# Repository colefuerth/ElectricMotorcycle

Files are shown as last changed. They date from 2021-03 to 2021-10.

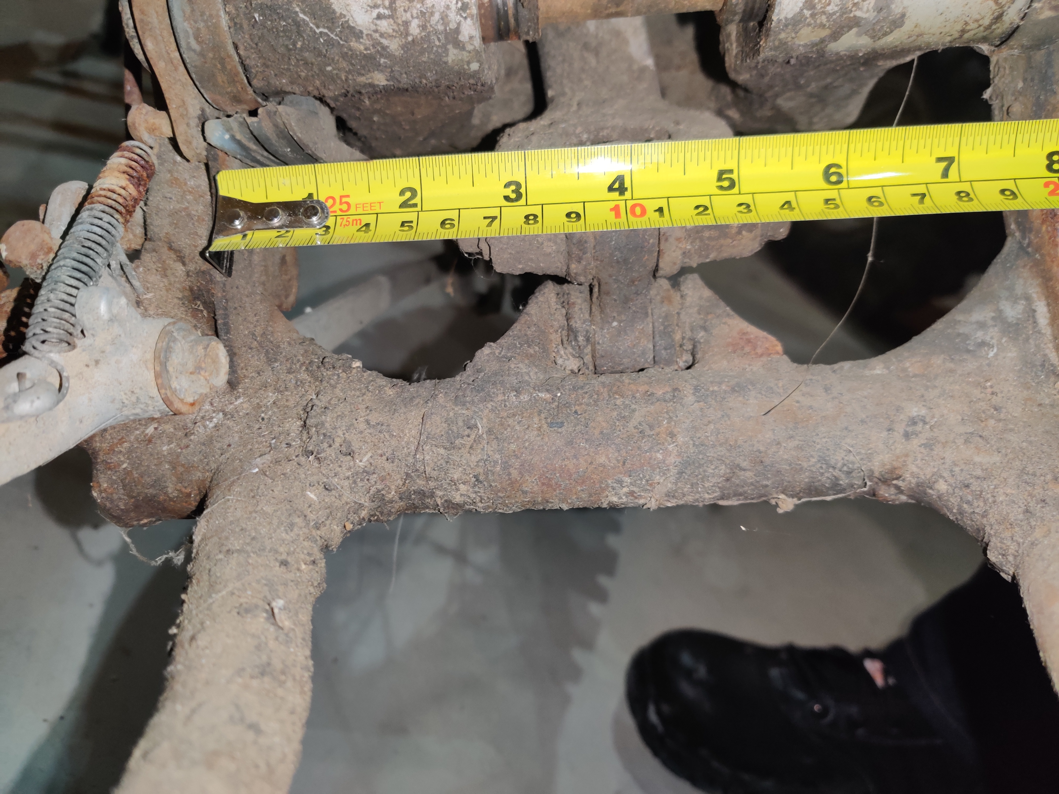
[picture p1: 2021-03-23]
Documentation/Mechanical/Mechanical pictures for Reference/IMG_20191113_204941.jpg

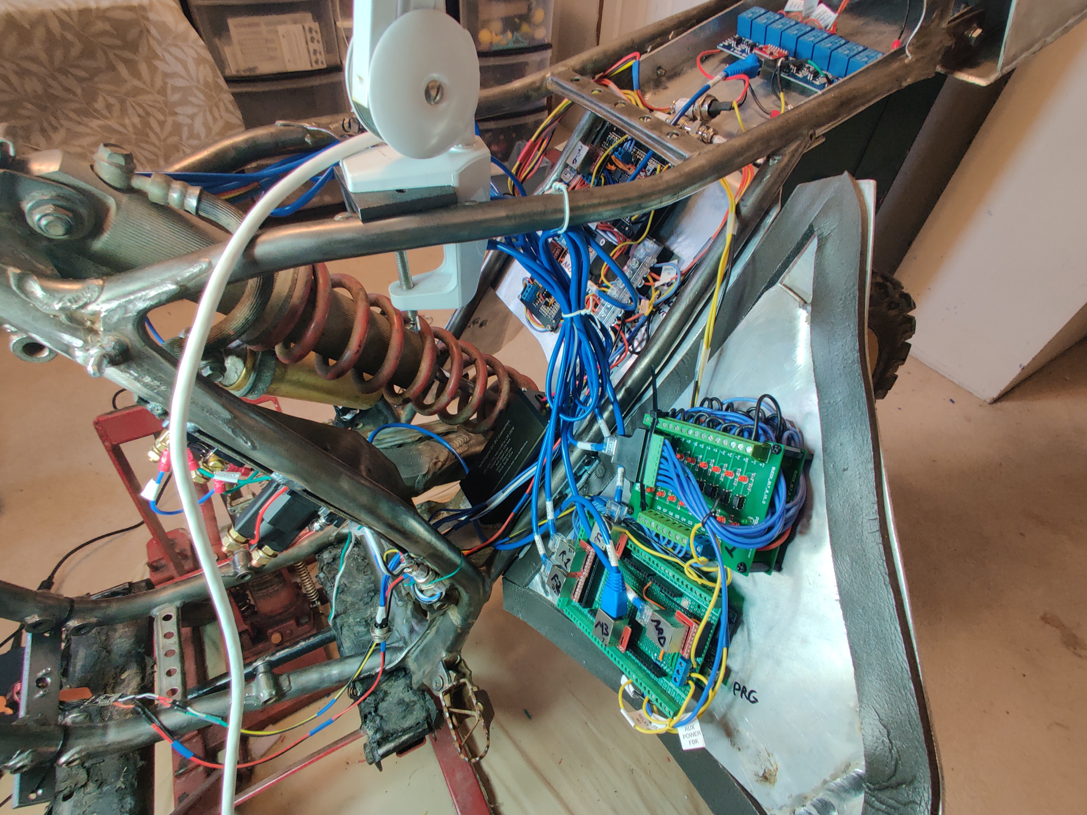
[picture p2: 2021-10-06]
Cole Fuerth Project Photo Repository/Wiring/Left view, panel open.jpg

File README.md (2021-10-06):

# ElectricMotorcycle

This was my Electronics Engineering Technology capstone project. 

A fully-electric dirtbike, built using an Arduino Mega.

### Key Features:
 * Fully-custom analog sensing boards, using OPAMPs and voltage protection for the Arduino
 * Custom firmware, written from scratch'
 * Electrical systems all designed by hand, with current safeties, and ALL IO is isolated in and out of the processor, to remove electrical noise.
 * Modular removable panels, with quick disconnects. Each panel comes off with four screws, and at most three connectors
 * Fully custom charging circuit and battery management
 * Touchscreen HMI, displaying telemetry and hosting a few settings, and a faults window
 * LOTS of faults, for communications, voltage, current, temperatures, safeties
 * Info prompts for when a safety stops the system from going into 'D' (drive)
 * Safety systems, disconnects on any major faults; main safety relay disconnects by a hardware-controlled switch, in case of processor lock-up
 * All lights and features required to make the bike road-legal

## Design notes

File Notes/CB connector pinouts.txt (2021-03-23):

PINOUTS FOR CB CONNECTORS

to arduino panel:
1 - GND
2 - ARD 5V
3 - 5V for HMI and RS3231
4 - spare

to central panel:
1 - GND
2 - 5V
3 - 12V to shunt input
4 - 12V rail

main power to central panel
1 - GND
2 - Vbat+
3 - motor shunt
4 - pwm motor control

cell levels
1 - cell 1
2 - cell 2
3 - cell 3
4 - throttle out

to rear fender:
1 - GND
2 - 12V
3 - 5V
4 - spare

to front panel
 - i didnt record these lmao

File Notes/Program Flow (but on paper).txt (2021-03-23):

-- PROCESSOR BOOTS --

<declare all variables>
	- include DS3231 libraries
	- define color values for nextion
	- define comm header byte for nextion
	- define serial port for nextion
	
	- declare function call memory bits (ONS,Timers,ToggledMemory)
	
	- declare arrays for opto inputs
	- declare constants for opto input pins
	- declare pointers into the opto arrays
	- declare speed px input and input pin

	- declare array for analog input values
	- declare constant arrays for analog input pin values
	- declare pointers into the analog data array

	- declare arrays for digital/relay outputs
	- declare constant arrays for relay output pin values
	- declare pointers into relay arrays

 	- declare misc variables for modes, clockRoutine, driveSystem, monitorSystem

	- declare a boolean array for active faults flags
	- declare a constant array for fault levels
	- declare a constant string array for fault messages
	- declare misc fault variables
	- declare pointers into the boolean fault flags array

	- declare misc variables for supporting my nextion functions in place of nextion libraries

	- declare misc debug bits and memory

-- PROGRAM START --

<SETUP>
	- check if aux 5v power is on, if off, processor disables all external IO

	- setup serial to PC if debugging is enabled
	- setup setial to nextion if nextion is enabled
	- setup RTC if aux power is detected

	- declare all IO pin modes (input/output)
	- write a 1 (relay off) to all relay output pins
	- put constant power on pins providing power/gnd to relay opto isolators

	- reset logic states on onshots, toggles, and fault flags

	- record the amount of time it took to complete setup and display to serial

	- do an IO update before starting the first scan

<LOOP>
	- Reset tracker bits for ONS and timers
	- set io update pulse (50Hz pulse triggers routine io updates)
	- Call MapInputs
	- call MapOutputs
	- call LightRoutine
	- call DriveSystem
	- call MonitorSystem
	- call HMIControl
	- call debugRoutine
	- call Faults
	- if firstscan, reset firstscan bit

<MapInputs>
	- if 50Hz pulse is true, do an IO update, else, update speed px state and return
	- every 50hz pulse, update all opto digital inputs and throttle analog value
	- every 50hz pulse, update one of the 7 nonessential analog pins, cycling through each time

<LightRoutine>
	- If lights are off, turn off all light bits, update horn status, and return
	- set turn signals using a flasher bit if their respective side is true
	- if a turn is false, front idles at true and rear idles at false
	- Set brake, headlight, and fog light outputs accordingly
	- set horn output accordingly

<ClockRoutine>
	- if aux power is on, update RTC value

<DriveSystem>
	- System will not go into gear unless:
		- killswitch has been off at least once since boot
		- killswitch is on
		- all essential connections are OK
		- throttle is at idle
	- check if killswitch has been off since boot
	- Main motor controller contactor will only be closed if:
		- killswitch has been off since boot
		- no level 1 faults are detected
		- killswitch is on
	- map throttle output based on ingear and killswitch statuses
	- map throttlePercent for monitoring/fault purposes based on throttle input value

<MonitorSystem>
	- record watchdog value
	- update longest/fastest cycle values
	- calculate current draw on motor and 12V shunts from analog IO
	- update total draw in mAh based on motor shunt reading
	- update vBat value
	- update individual cell volt values
	- update front wheel speed from speed PX

<HMIControl>
	- check for button presses from nextion
	- update fault window buffer
	- update elements on the current page only, one at a time on a 50hz pulse, and only update if the value has changed from the last update on that element, or if the current page has changed since the last update on that element

<MapOutputs>
	- Update outputs if:
		- an IO update request pulse is read
		- aux power is on OR debugging is enabled

<Faults>
	- Check for a fault reset request, if true, reset all fault flags
	- check for com errors to opto boards, or either side handlebar controls
	- check watchdog (set for 100ms)
	- check that throttle value is within bounds (0.5V to 4.5V)
	- check for overflow on ONS bits
	- Check that individual cells are above lithium storage voltage, else throw a warning
	- Check that individual cells are above lithium critical voltage, else throw a level 1 fault
	- check for any faults present
	- check for any level 2 faults present
	- check for any level 1 faults present
	- count number of active faults
	- display faults to serial if debugging is active on a PET
	- check if aux power has failed
	- check if number of timers or oneshots has changed since previous scans, if yes, throw a level 1 fault
	- if first scan, record values of timer and ONS tracker bits at the end of scan

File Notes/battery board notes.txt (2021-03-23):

heaters blow at constant current over 3A

If I use these in 6S, 4P:

6*16 = 96V

3A * 4 = 12A

96*12A = 1152V

 - using the thermocouples is NOT an option; they will blow all the time
 - ktm e-xc is 3.9kwh and lasts about an hour and a half; 3.9kwh / 1.5h = 2.6kw
 - 2600kw / 96v = 27A constant current
27A / 4P = ~7A
27A / 5P = 5.4A constant

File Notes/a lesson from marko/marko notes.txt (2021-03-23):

CA3140E single ended opamp pin compatible with lm741

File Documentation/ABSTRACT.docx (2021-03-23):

ABSTRACT

The EET Capstone project, “Control System for an Electric Motorcycle”, is a project designed to control a fully electric motorcycle, with lithium-ion cells, a charging circuit, an electric motor/controller, and safety and monitoring systems using an Atmega 2560 processor. This system uses amplifiers, optocouplers, relay boards, voltage converters, an EV controller, lithium balancing circuits, and several more systems to create a ‘smart’ system for monitoring the status of the system. Both the user via the physical killswitch, or the processor, with a relay killswitch, will be able to disconnect the battery from the EV controller. Individual monitoring systems on-board include:

- Current monitoring of a 12V supply
- Current monitoring of total draw from battery, up to 150A
- Monitoring of individual cell voltages, each cell is 4S lithium, and 4 of those in series
- Monitoring of total current draw from the battery in mAh
- Monitoring of the front wheel speed
- Monitoring of the total battery voltage
- Monitoring and recreation of the throttle value

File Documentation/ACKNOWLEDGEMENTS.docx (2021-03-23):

ACKNOWLEDGEMENTS

There are a few key people that were important in the design and fabrication of this project.

First, my friend Scott MacKay, who was around for the entire mechanical build of the project; he did most of the cutting and shaping of aluminum and steel, and all of the steel welding. The panels would not have turned out as well as they did without his help, and he was around for many, many hours during build.

My father, Brian Fuerth, welded the rear fender, and cut the front panels where the headlights and charging circuits are. He took an interest in the mechanical construction, and he will be helping with construction of the drive system of the bike, including motor and controller mounts, and a chassis for batteries.

Al Repmann is another individual who helped, he did most of the aluminum welding with his spool welder and some Tig welding.

Marko Jovonovic and John Schlichther were some individuals I consulted on opamp design, which were issues I would not have been able to efficiently tackle myself.

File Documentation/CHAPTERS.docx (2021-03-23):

Introduction

My name is Cole Fuerth, and for my Electronics Engineering Technology capstone project, I built a control system for an electric motorcycle. This project, unlike most of its peers, does not have a set cycle or repeated function. Instead, my system monitors ongoing telemetry, and uses input from the user and peripheral devices, to safely control an electric vehicle, with some safeties, and a basic throttle control. This system monitors total battery voltage, as well as the voltage of individual lithium cells, and the current draw of the total system from a 60VDC source, and the current draw of the control system at 12V.

The biggest challenge of creating this system is creating a safe and reliable interface between a 5V TTL ecosystem, a 12V control system, and a 60V drive system. Instrumentation amplifiers and operational amplifiers are used for measuring and isolating analog input and output signals with the Arduino Mega controller, and opto-isolators isolate the 12V inputs, while opto-isolated relay packs handle 12V output control, and some control of the EV Controller functions, in place of switches.

Much effort was put into hardware safeties. One of these important features is the ability to monitor individual cell voltages. Lithium cells can be dangerous when misused, so if a heater safety is tripped on a cell in parallel with others, or one cell has a much higher internal resistance than others, the load is not evenly distributed, and there is a discrepancy between capacities of the cells in series. This can become a big problem in the short and long term, as it is important all the cells wear evenly in a system with 200 lithium cells networked together.

Overall, I am very proud of this achievement in creating this project, and although the conclusion of the Capstone approaches, this system will continue to grow and improve as its use continues long past the conclusion of EET 617.

System Design:

Processor Logic Layout

Since the processor needs to handle and map a large volume of information within and outside its architecture, arrays were used for data handling, and referenced locations within these arrays by defining pointers into the arrays to access information when it was needed. This proved to be a very effective system, as the code was very messy and hard to understand before this system was implemented. This allowed handling of all the IO at once when mapping inputs and outputs, by defining arrays in global memory for storing the status of bits and integers being used, along with their corresponding hardware pins when applicable.

Within the main program loop, all logic is done within subroutines, and all subroutines are called within the loop. This allows the separation of logic into routines with a specific task, so one task can be skipped according to user settings, for example, the LCD display can be disabled in settings.

The program starts with importing libraries for the DS3231 (Nextion libraries were scrapped, and replaced with methods that were developed (because the stock Nextion methods were too slow), then definitions, followed by all global memory declarations, including arrays, settings, and pointers into arrays, and misc global memory used to support methods, and then the main program flow. The program starts by running the setup() method, which sets up auxiliary devices and digital IO based on user settings and feedback from auxiliary power, and sets any status bits that need an initial value before the main program cycle begins. After setup completes, the processor begins looping the loop() method, which calls all of my methods I created to handle the vehicle functions.

Methods

Many processes within the logic are repetitive, so methods were created to promote efficiency. A method is a section of code that can be called with or without parameters, that returns either void or a variable defined with the method. This resulted in much cleaner memory management, and an easier to understand program. A good example of this format is my OneShot logic. There are 32 globally available oneshot bits, as well as 32 dedicated to each fault, for displaying fault messages once when a fault goes true. OneShot are managed automatically, with a tracker that is reset at the end of every cycle, and every time a oneshot is called, that bit is incremented, so the call will adapt to the number of oneshot calls used.

Other calls were created for things such as writing Nextion values and settings, whose process is detailed below in the Nextion HMI Display section.

Other examples of methods created are voltage to analog translations, which would be able to convert back and forth between floating point voltages, and integer values for either analogRead or analogWrite values, an on timer, or ‘TON’, a limit method that returned a Boolean, similar to that used in PLCs, and methods for addressing button presses on the HMI.

There also exist methods for returning string values; one is called every scan and cycles through active faults, to be displayed on general information pages at the top in a fault window, and another generates a list of the top 10 active faults sorted by priority, which can be returned individually by requesting spot 0-9, to be displayed in a list of faults on a window in the HMI.

Fault Handling

A Fault-oriented safety system handles safety processes, with a motor contactor that can break the connection between the battery and the EV controller. This connection is broken either by the processor via a relay when a Level 1 (Highest level) fault, or a throttle input exception is detected. The contactor coil is connected in series with a control relay, and a kill switch on the handlebars, so that if the processor freezes, the user still has a hard-stop to kill power to the motor. A level 1 fault is defined by a critical program fault in my functions, such as a miscount of automatically handled functions like ONS or Timers, or connection via RJ45 to the handlebars is lost, or throttle input leaves the acceptable range. A level 1 fault is a fault that requires a disconnect of power to the EV controller. The processor uses a watchdog to ensure IO updates are occurring fast enough to be reliable, and if deemed unreliable, throws a level 1 fault.

Faults are handled with an array of fault flags, differentiated by pointers that point to their memory bit within the array. Parallel arrays to the fault flag array contain information on fault level, as well as a message to go along with the fault when it is flagged.

Analog inputs

Operational Amplifiers were used for analog signal isolation in and out of the processor, chosen for their reliable electrical isolation between input and output, and their ability to only repeat an analog voltage within the supply rails.

A stack of custom soldered breadboard circuits handles all analog signals between the Arduino processor and the rest of the system. This includes total battery voltage, voltage on each of the four 4S Lithium cells in series that make up the battery, signal levels from the two current shunts, and throttle input and output levels.

Current levels are determined using current shunts, which are very low resistance resistors, that are made to an extreme level or precision, and to a certain spec. An example of this spec would be, that my 12V shunt is rated to 75mV at 15A across the shunt. This means, when the shunt is passing 15 amps of current, it will cause a potential drop of 75mV. This potential difference is the analog signal that is processed by my stack.

Analog values are processed by Instrumentation Amplifiers in the stack. The type of amplifier used was an INA126P. This amplifier is fed rail voltages of +16V and -9V, so that any and all analog readings on the input pins are well within the rail voltages, ensuring accuracy. The default gain on an INA126P is 5, and the output potential of this package can be represented by: V_(out) =(in_(+) -in_(-) )*(5+(80kΩ)/(R_G)) . In the case of a very low input differential, getting an accurate and useable output means we need a gain resistor, R_G . R_G was calculated for the 12V shunt, for example, by substituting the maximum current reading signal level as the voltage differential, and the maximum output potential desired on the Arduino input as V_(out) (4.50V), and solving for R_G . The closest value to the result that could be produced with the parts on hand was 1.47kΩ , which would produce a potential of 4.425V at 15A through the shunt. A similar process was followed for the 50mV 150A shunt for measuring current directly at the battery negative terminal, which calculated an R_G of 1kΩ .

Voltage levels on individual cells were collected using INA126P amplifiers and voltage dividers. Each cell node was divided, so that the four levels, spanning from ground to cell 4, were at a potential of 3.4V. This meant that, the potential drop across each cell after the voltage divider was about 0.85V. After using these references to generate a signal for each cell voltage through INA126P Instrumentation Amplifiers, the optimal signal level for each cell was approximately 4.25V. This level is easily and accurately able to be read and mapped to a real voltage level for the Arduino to use, and display to the user.

The schematic of the four cell voltage sensors:

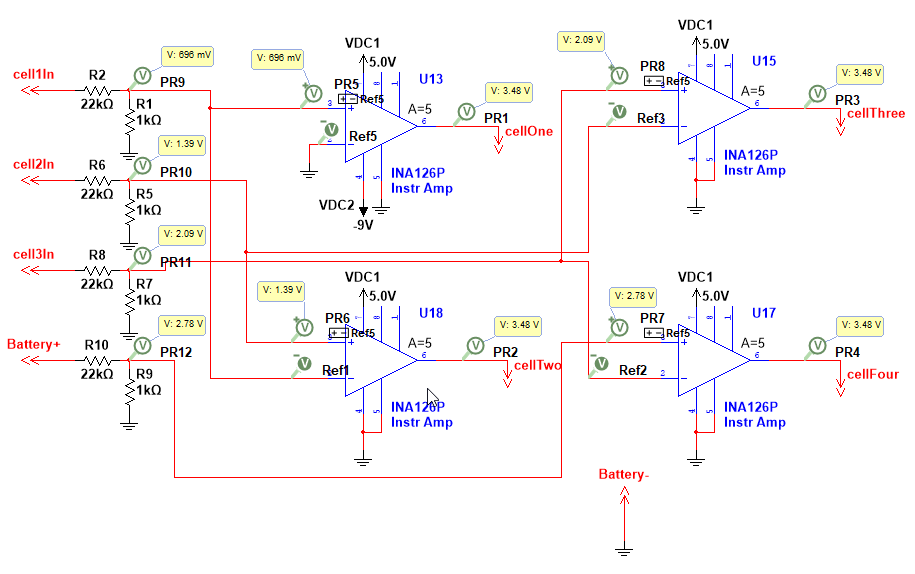
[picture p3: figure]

Figure 5-1

The total battery voltage was read using a voltage divider, same as above, so the battery voltage signal at 68V (charged), was 3.4V.

All analog inputs were buffered through CA3140 op amps, which provided reliable electrical isolation, and are linear op amps matching the pin configuration of LM741s, while being able to reliably operate close to the rail voltages, making them very useful as buffers.

The EV controller

The EV controller used was a 9kW CA Controller. This controller operates between 48V and 100V DC, and controls a brushless motor. The inputs of this controller include an analog throttle reading of 1-4V, as well as wires used for selecting modes of operation by grounding the connections. The throttle signal is provided by a high-frequency (980Hz) PWM using duty cycle to control the DC level, which is passed through a CA3140 linear operational amplifier and a 2N4244 NPN transistor to provide electrical isolation, and a power amplifier capable of delivering up to 500mA. The controller does not sink this much current, but a CA3140 can only source 14mA of current, so a power amplifier circuit was implemented to avoid stressing the analog buffer. Control of the mode selection was accomplished using a relay pack dedicated to ESC control, which operates the motor contactor solenoid, as well as shorting out control wires as mentioned previously.

Light Control

Lights are controlled by 6-channel relay packs, at the front and rear of the vehicle. Lights all operate at 12V DC, and are controlled by the Arduino, using switches on the handlebars of the vehicle. The bike features a headlight and taillight, brake light, front and rear turn signals, and fog/trail lights. Some features unique to this bike from others is, most two-wheeled vehicles do not feature hazard lights or fog lights, or a master kill switch for lights, but these were implemented in this system. Fog lights are used at night, to light up the operator’s peripheral vision. The light kill switch is useful for power conservation, and it never hurts to be sneaky, especially on an electric vehicle, when noise is already at a minimum. Turn signals were added so that the vehicle could be safe when passing though an urban environment.

Speed Sensing

Speed sensing is done using an inductive proximity sensor picking up spokes on the front brake disc. The front wheel has a 70cm outer diameter, and there are 8 spokes on the disc. Using the outer diameter, the wheel RPM was calculated at different speeds, and then using that information, the positive pulses per second could be determined at different speeds. The points found were at 100km/h, the wheel rotates at 12.64RPM, and generates 101 pulses per second, so ~10ms between each pulse, and at 25km/h, there would be 40ms between each pulse. A map() method was used with these two points for reference, since the relation is linear, to generate a value in km/h by measuring the time between each positive edge trigger from the PX to calculate the speed of the front wheel.

Nextion HMI Display

Design of the HMI display took a long time, as the system started with attempts to use a TFT display, driven by an Arduino Mega. This approach proved inefficient, so a different platform was adopted. Nextion is a very polished system, in relation to its competitors in the Arduino community, and proved to be easy to develop, thanks to its GUI interface for development. The stock Nextion libraries were unreliable and slow, so custom libraries were developed by studying how the default libraries would handle incoming and outgoing data, and replicating that serial format to create custom libraries designed around the vehicle’s ecosystem. This method proved much faster and more reliable, and stopped the processor from ‘hanging’ during serial transfers, like it did when using the stock libraries.

The Nextion display has three screens: a main screen, an alarms screen, and a statistics screen. The ‘MAIN’ screen only displays essential information in a larger font, for ease of use on the go. The ‘ALARMS’ screen displays up to ten active alarms, in order of importance. The ‘STAT’ screen displays more information than the main screen, in a smaller font, for active monitoring of telemetry within the system.

The system is optimized such that, only elements on the current page are updated, and only one element is updated at a time. Elements are also only updated when the value changes from the previously written value, using a buffer. Further optimization was achieved by changing the BAUD rate on the Nextion from 9600 to 115200, using a custom method.

Drive Safeties

The vehicle was designed such that, in order to arm the vehicle, a certain set of conditions must first be met. Firstly, the kill switch must be on. Secondly, the kill switch must have been in the ‘open’ position at least once since boot, to prevent accidental arming on boot. Thirdly, the throttle must be at idle when the start PB is pressed, in order to arm the motor. Any level 1, or ‘critical’ faults, will automatically open the motor contactor.

Charging Circuit

A charging circuit was implemented, to avoid disassembly of the battery pack for charging. Each 16S pack is made up of four 4S Li-Ion packs in series, so when in operation the pack operates as a 16S 5200mAh battery pack, but when in charging mode, an 8-channel relay board is provided power, and all four of the 4S packs switch into a parallel configuration, on a different connector than the one used for normal operation. This allows for charging of all the packs at once, without disassembly of the entire battery assembly. When no power is applied to the relay packs, the pack defaults to the NC contacts, and the pack is once again in a 16S series configuration.

A dedicated 5V rail and charging rail are entirely isolated from the normal, operating circuits, so in charging mode, the cells are completely disconnected from the system.

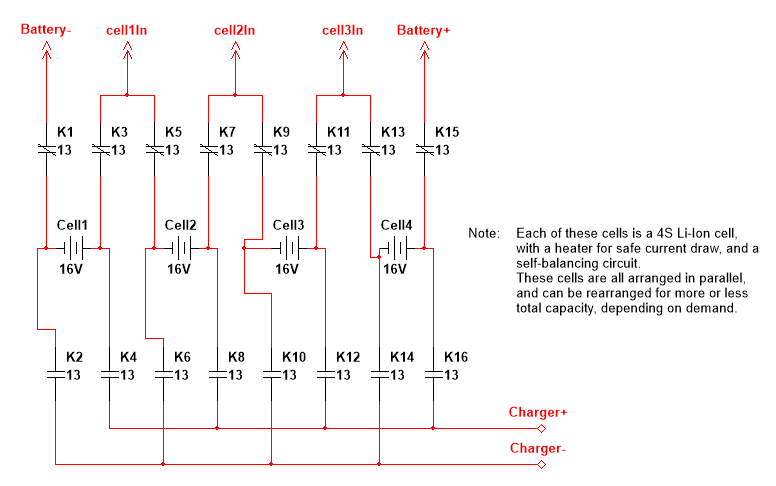
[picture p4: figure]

Figure 8-1

Background Theory:

Instrumentation Amplifiers

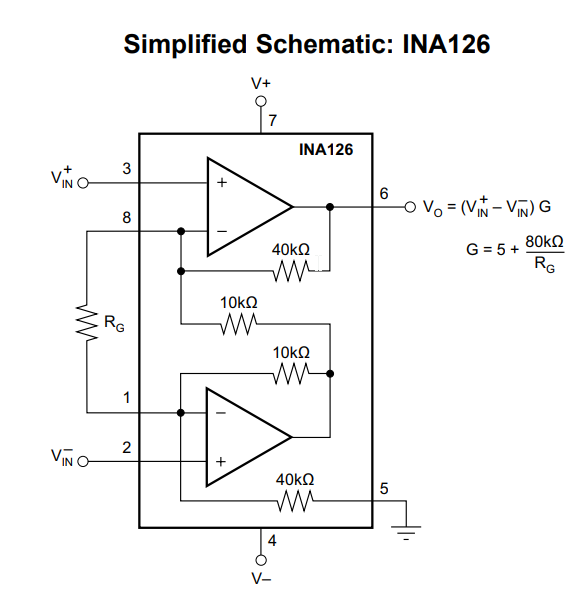
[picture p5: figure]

An instrumentation amplifier is a type of operational amplifier that produces an output signal proportional to the difference between two input pins. The instrumentation amplifier used was an INA126P, which is an 8-pin op-amp package, which has a pin configuration compatible with standard solderable boards, or breadboards. Both inputs must be within a ±0.7V range outside of the supply rails, so a negative and positive supply greater than the range of inputs is recommended, but the INA126P is a package capable of single-ended operation, meaning that the negative supply rail can be grounded, and the package will still behave reliably. The package is capable of up to ±18V supplied, or a 36V difference in potential between the supply rails.

Figure 9-1

Output potential on pin 6 of this package can be calculated with the formula:

V_(out) =(in_(+) -in_(-) )*(5+(80kΩ)/(R_G))

R_G is a gain resistor, connected across pins 1 and 8. With no gain resistor, this package defaults to a gain of 5, but when a higher gain is desired, output can be amplified. This is especially useful when conditioning a signal from a current shunt.

Linear Operational Amplifiers and Power Amplifiers

The CA3140 Operational Amplifier is a package matching the pin configuration of an LM741, but able to reliably operate on a single-ended supply, and still reproduce an analog signal near the voltage supply rails. This characteristic is imperative in an analog buffer or power amplifier.

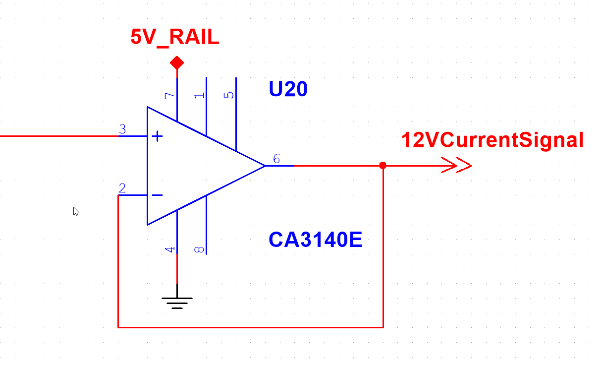
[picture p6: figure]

The CA3140 operates on a supply of up to 36V across the supply rails but is rated to operate reliably in a 5V TTL system.

The CA3140 can be configured as an analog buffer using the following schematic:

Figure 10-1

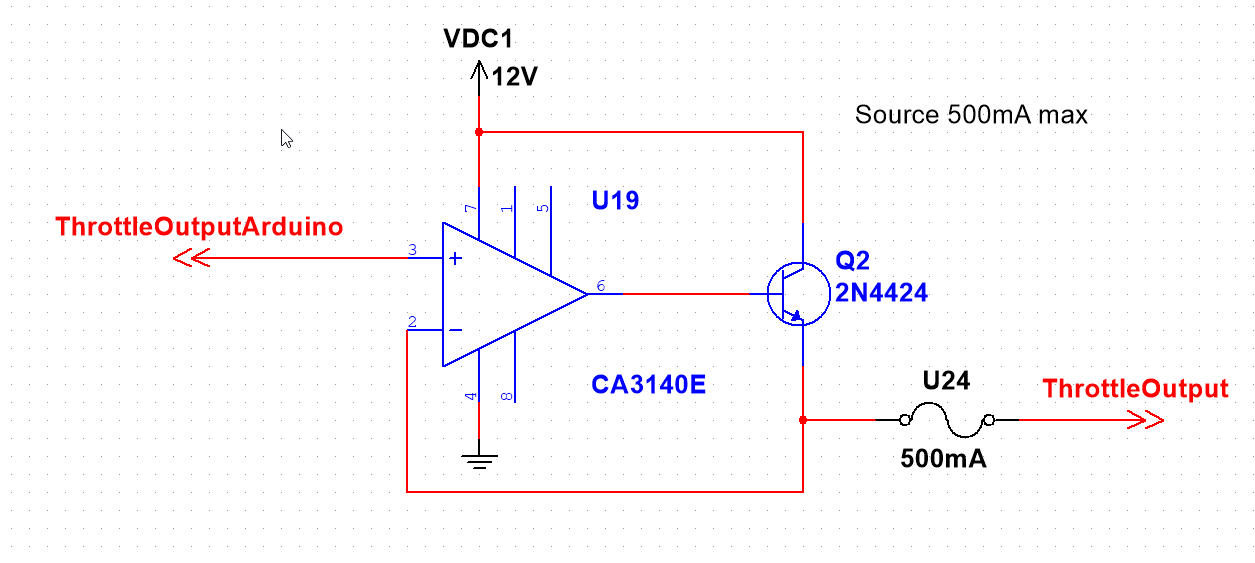
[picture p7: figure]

The CA3140 can only source up to 10mA maximum in a 5V TTL environment, so in a situation where this package is used as a voltage out buffer into a larger system, a power amplifier circuit is useful. Connecting the emitter of an NPN transistor package to the feedback (-) pin of the CA3140, the output of the package to the base of the transistor, and the collector of the transistor to the supply rail of the package produces a current supply of whatever the transistor is capable of, with the precision and isolation of the CA3140. This functionality can be accomplished with the following schematic:

Figure 10-2

The 2N4424 Transistor package is an NPN transistor capable of sourcing up to 500mA, so in this configuration, a TTL processor can provide a PWM DC signal via pin 3 on the CA3140, and have electrical isolation from the output, along with a 500mA current source available, should it be needed.

Voltage Dividers

A voltage divider is a small, simple circuit that typically ‘divides’ a large signal into a smaller, useable signal. In this application, voltage dividers are used to sample battery voltage levels, and step them down to a level able to be processed by TTL circuits.

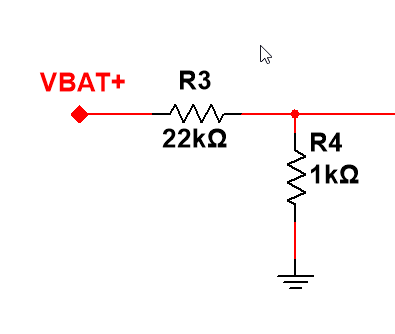
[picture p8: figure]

A voltage divider can be represented by the equation: V_(out) =V_(in) ((R_1)/(R_1 +R_2)) . For example, the total battery voltage is 68V, so the voltage divider used was R_1 =1kΩ , R_2 =22kΩ . This meant, the 68V input potential is reduced to 2.96V, which is well within the range of analog voltages handled in a TTL environment.

Figure 11-1

Opto-Isolators and Relays

Opto-Isolators and Relays are useful IO interfaces between a processor and external components in a control system. Opto-isolators utilize LED lights and photodiodes to provide complete electrical isolation between a processor and a control system, while operating at extremely fast speeds. Opto-isolator connections are typically active-low, meaning that when no potential difference is present across the inputs, the output to the processor is a TTL 1, but when a signal is detected at the input, a TTL 0 is sent to the processor.

Relays can be used together with optocouplers to provide two levels of isolation: The first level is the opto-isolated logic input from the processor, where a LOW signal is considered a logic TRUE. Then, an auxiliary power supply (5V, in this instance), will provide power to the relay coil when a TRUE signal is received, energizing the coil. The contacts on the relay can then operate up to a 250V / 10A control, providing complete isolation between the processor, 5V supply, and 12V control circuit.

Nextion HMI Libraries

The Nextion 3.2” Standard model was used as an HMI display. This model uses a GUI to design the interface, where different types of elements can be placed. These elements are each given an elementRef and a number to identify which element is which.

Serial communication to the Nextion is conditioned manually via a custom method, as the stock Nextion libraries are buggy.

A typical message to Nextion to set a ‘text’ of elementRef ‘t0’ is conditioned as follows:

‘t0.txt=”test”’ is sent using a Serial.print() command, followed by three Serial.write(0xFF) commands to signify the end of a message. All elements are set this way, by sending strings over serial to the Nextion followed up by ‘0xFF’ three times, which is then interpreted by the Nextion as a command.

Some other examples of Nextion commands used are:

Command | Descripton
baud=115200 | Sets the serial baud rate to 115200
t0.txt=”test” | Sets text element “t0” to “test”
b0.val=20 | b0 is a progress bar, which accepts any integer between 0-100
t0.pco=0x07E0 | t0 text element font color is set to green

Table 12-1

Nextion also sends serial messages to the Arduino on event of a button press, if the checkbox “send component ID” is checked for either a press or release event. This message is structured such that:

- Message begins with 0x65
- Three bytes follow the initializer, which represent, respectively, the page number, component ID, and event type (always 0x01 for button presses)
- 0xFF received three times in a row signifies the end of a message

Monitoring the serial buffer for messages in this configuration allows the processor to interpret serial messages from the Nextion HMI.

Conclusions:

Overall, this project, “Control System for an Electric Motorcycle”, although not perfect yet, has evolved over time. The initial features planned are mostly nonexistent here, replaced with equally advanced, if not more advanced, features that were deemed more important to operation.

Initial pulse check for light operation was removed and replaced with monitoring of the individual 4S cell voltages making up the battery pack. Odometer tracking was removed, as it is unimportant in an off-road vehicle, and was replaced with more advanced safety systems and faults.

One feature that was not finished because of hardware issues, was SD Card logging. This feature, although not present at the time of submission, will be completed later, as it is essential to debugging once the vehicle is in active use.

The panels and electrical build did turn out better than expected. The panels are sleek and formed to the shape of the frame and provide ample space for any and all electrical components mounted inside the frame.

Due to issues with suppliers, the drive motor and controller have not yet arrived, and will not be present at the time of demonstration and will be replaced by a small drone motor and controller, for demonstration purposes.

The system does have full lighting controls, as well as safe, isolated IO on the processor. Other features that were successfully implemented include analog sensing on electrical circuits throughout the vehicle, including 12V and Motor current readings, as well as total battery power and monitoring of individual 4S cell potentials within the 16S pack.

A lithium charging circuit was developed, built-in to the custom packs, to remove the need for disassembly when charging. This auto-switching charging circuit is a massive quality-of-life improvement.

The program is the largest section of the project; many standards were developed for it, and it has undergone 7 months of constant growth, refinement, and optimization. Although there are still some bugs and issues, they will continue to be addressed and this system will grow beyond the conclusion of this project.

References:

- Nextion send and received logic was copied from the Nextion master library, provided by Nextion on GitHub, and modified for efficiency and speed within the vehicle’s ecosystem. Core concepts of the code, although interpreted and structured using custom methods, and not exactly the original, were created by Nextion.

Bibliography:

- Nextion logic and examples were used to develop custom Nextion serial functions
- DS3231 Libraries were used for generating a time value from an RTC

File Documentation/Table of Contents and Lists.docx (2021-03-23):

Table of Contents:

Page | Section
i | Letter of Transmittal
ii | Title Page
iii | Declaration Page
iv | Table of Contents
v | List of Figures
vi | List of Tables
1 | Acknowledgements
2 | Abstract
3 | Introduction
4-10 | System Design
11-14 | Background Theory
15 | Conclusions
16 | References
17 | Bibliography
18-29 | Full electrical drawings
30-34 | Panel layouts
35-39 | Pin designations
40-41 | BOM
42 | Block Diagram
43-54 | Program flowcharts
55-78 | Full program listing

List of Figures:

Figure 5-1: | Schematic of Cell voltage sensors using Instrumentation Amplifiers and Voltage Dividers
Figure 8-1: | Battery pack schematic
Figure 9-1: | Simplified schematic of an INA126P Instrumentation Amplifier package
Figure 10-1: | Simple schematic of a linear op-amp buffer
Figure 10-2: | Schematic of a linear op-amp/transistor power amplifier/buffer
Figure 11-1: | Schematic of a voltage divider

List of Tables

Table 12-1: Nextion HMI commands used in the program

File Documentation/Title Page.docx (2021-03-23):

Control System for an Electric Motorcycle

EET 617 Progress Report

March 26, 2020

Cole Fuerth

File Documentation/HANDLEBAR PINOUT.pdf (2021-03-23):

ST. CLAIR COLLEGE DRN BY CLASS TITLE DATE SCALE C.C.F 001 JAN'20 FULL HANDLEBAR PINOUT LH HAND CONTROLS RH HAND CONTROLS COLOR DESCRIPTION GRN/BLK LEFT TURN OUTPUT GRN/WHT RIGHT TURN OUTPUT ORANGE TURN SIGNAL POWER LBLUE OUTPUT TO LOWBEAM BLUE OUTPUT TO HIGH BEAM RED/WHT POWER FOR HI BEAM TRIGGER / DUAL LIGHT BRN HORN OUTPUT YELLOW/RED POWER FOR HI/LOW HEADLIGHT ORANGE/RED OUTPUT FROM CLUTCH SENSOR COLOR DESCRIPTION RED KILLSWITCH OUPUT YELLOW/RED LIGHTS ON OUTPUT YELLOW FOG LIGHTS OUTPUT GREEN/YELLOW START PB OUTPUT BROWN/YELLOW POWER FOR START PB & KILLSWITCH RED/WHITE POWER FOR BRAKE AND FOGLIGHT PURPLE FRONT BRAKE OUTPUT YEL GRN/YEL YEL/RED PUR RED/WHT BRN/YEL RED GRN/BLK YEL/RED BRN RED/WHT LBLU ORA ORA/RED BLU GRN/WHT

# PRODUCED BY AN AUTODESK STUDENT VERSION PRODUCED BY AN AUTODESK STUDENT VERSION

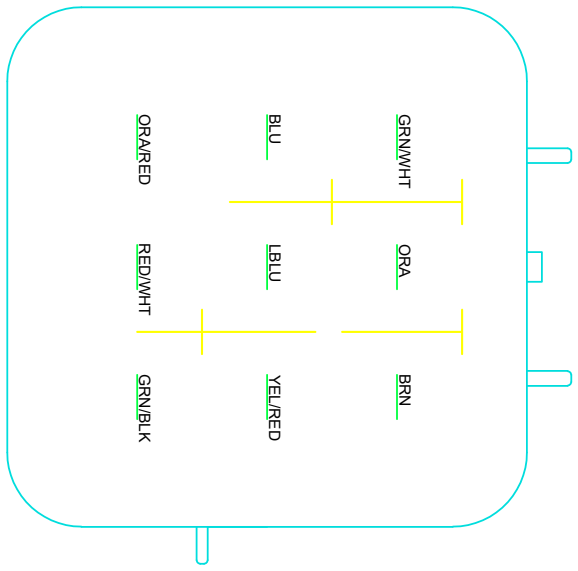
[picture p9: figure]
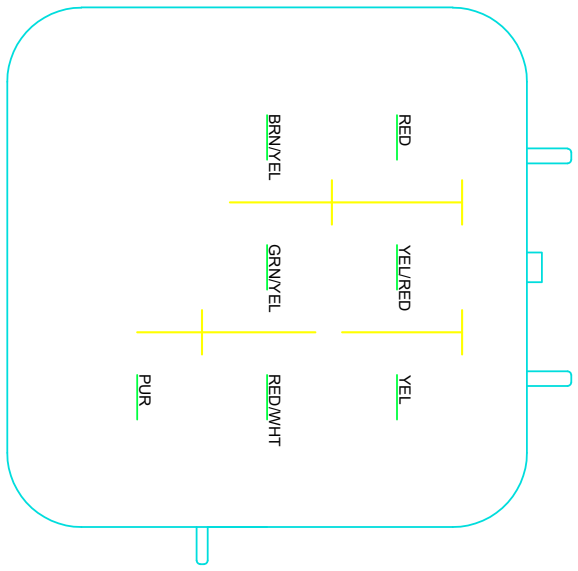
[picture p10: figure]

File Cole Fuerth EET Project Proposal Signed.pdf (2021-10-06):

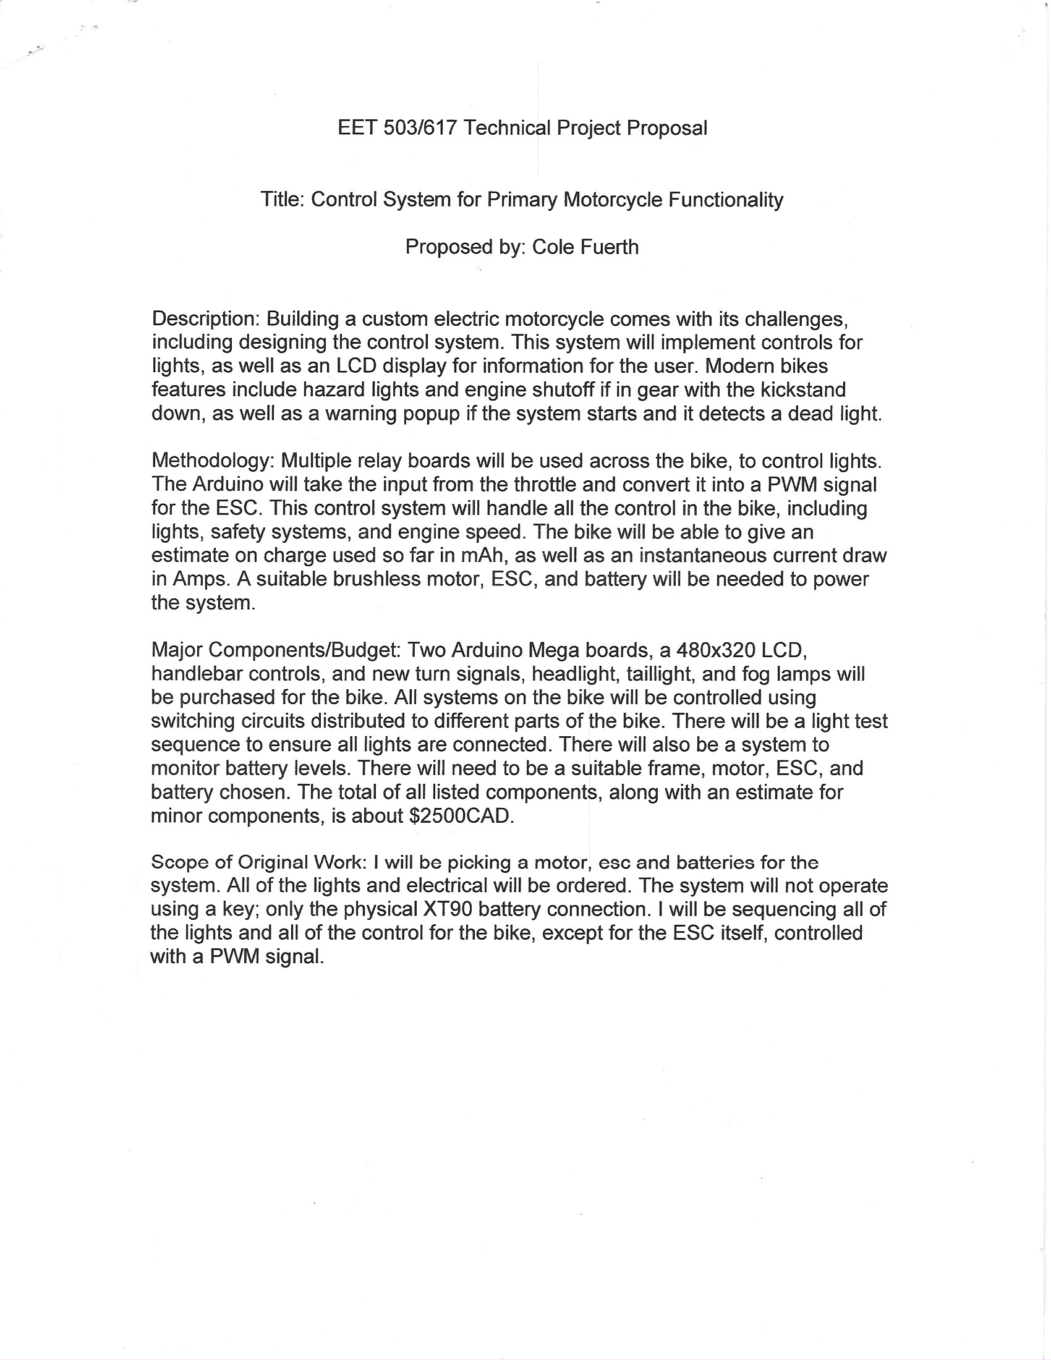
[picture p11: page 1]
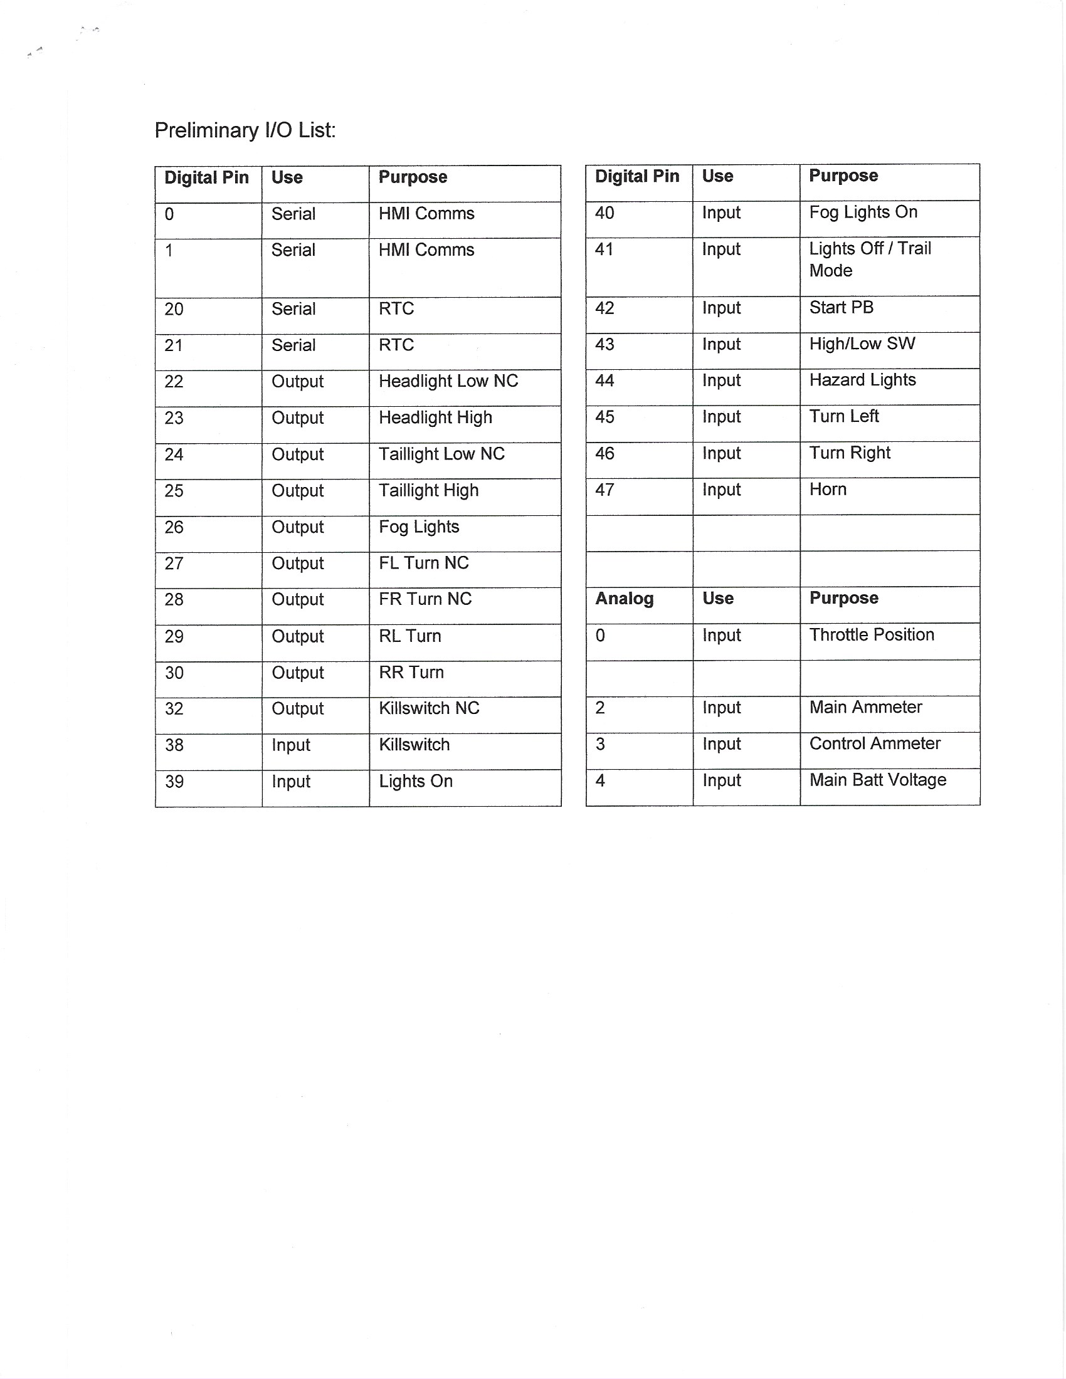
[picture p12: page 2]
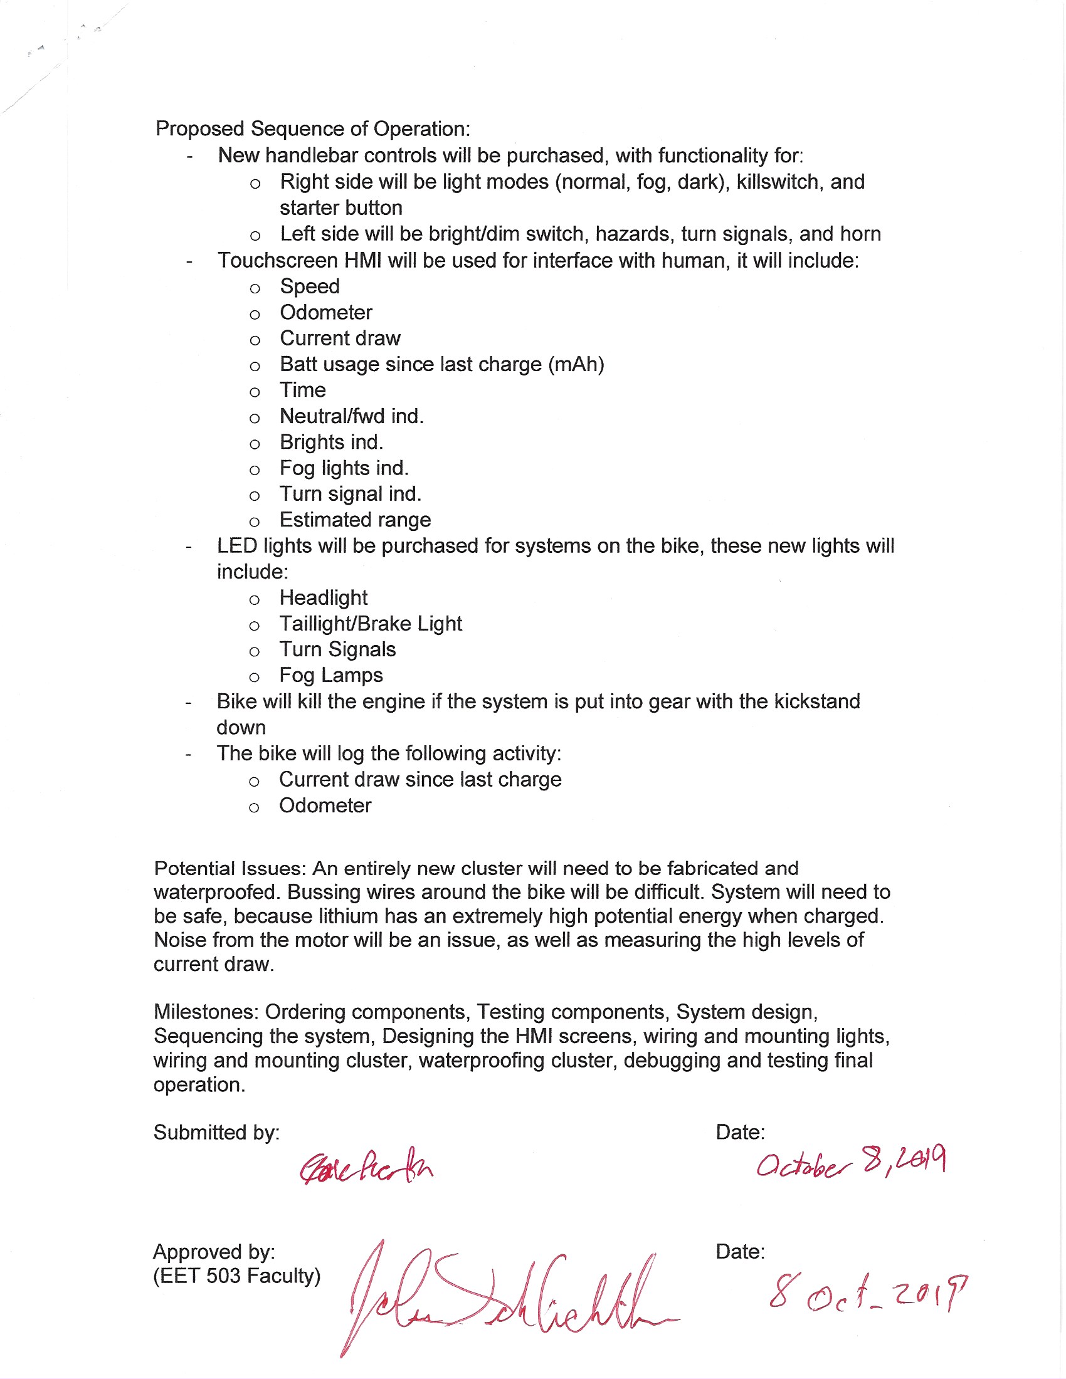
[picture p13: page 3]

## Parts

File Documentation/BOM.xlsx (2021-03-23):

Bill of Materials
Control System for Electric Motorcycle
Cole Fuerth
Description | Qty | Price per unit | Subtotal | Supplier
YZ125 Dirtbike (Used) | 1 | $360.00 | $360.00 | Facebook Marketplace
324 18650 batteries, 4s packs | 1 | $200.00 | $200.00 | Facebook Marketplace
15kW 100kV Brushless Motor | 1 | $560.00 | $560.00 | Alien Power Systems
9kW 60V EV Controller | 1 | $550.00 | $550.00 | Alien Power Systems
Hall Effect Throttle | 1 | $10.00 | $10.00 | Alien Power Systems
150A shunt | 1 | $30.00 | $30.00 | Digikey
Handlebar Controls (L&R) (https://www.aliexpress.com/item/32825374071.html) | 1 | $23.54 | $23.54 | AliExpress
Fog Lights (2) (https://www.aliexpress.com/item/32817324207.html?spm=a2g0o.cart.0.0.7b8b3c007ioiuo&mp=1) | 2 | $22.66 | $45.32 | AliExpress
Turn Signals (4) (https://www.aliexpress.com/item/32811500453.html) | 2 | $7.98 | $15.96 | AliExpress
Arduino Mega (https://www.aliexpress.com/item/32665372585.html) | 2 | $8.32 | $16.64 | AliExpress
Nextion 3.2" (https://www.aliexpress.com/item/33037936383.html) | 1 | $46.99 | $46.99 | AliExpress
RTC | 2 | $0.93 | $1.86 | AliExpress
12V-5V 3A regulator | 2 | $1.44 | $2.88 | AliExpress
15A Shunt (https://www.aliexpress.com/item/4000064064917.html) | 1 | $3.02 | $3.02 | AliExpress
18AWG Assorted Wire (https://www.aliexpress.com/item/32958017642.html) | 1 | $15.20 | $15.20 | AliExpress
sdcard reader (https://www.aliexpress.com/item/32912448654.html) | 1 | $0.74 | $0.74 | AliExpress
Arduino Mega Screw Terminal Shield (https://www.aliexpress.com/item/32822652489.html) | 1 | $14.00 | $14.00 | AliExpress
M3 Hardware Kit | 1 |  | $0.00 | AliExpress
10x xt60 connectors | 1 | $2.54 | $2.54 | AliExpress
8CH 12V to 5V OPTO Board (https://www.banggood.com/8-Channel-12V-To-3_3V-Optocoupler-Isolation-Module-PLC-Signal-Level-Voltage-Conversion-Board-p-1336505.html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) | 2 | $14.59 | $29.18 | Banggood
30pcs PCB Screw Terminals (https://www.banggood.com/30pcs-5mm-KF-301-3-Pin-PCB-Mount-Block-Screw-Terminal-NF-Connector-p-1189488.html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) | 1 | $6.43 | $6.43 | Banggood
inductive proximity sensor (https://www.aliexpress.com/item/32849210989.html) | 3 | $3.00 | $9.00 | Banggood
INA126P Instrumentation Amp (https://www.digikey.ca/product-detail/en/texas-instruments/INA126P/INA126P-ND/254672) | 8 | $4.80 | $38.40 | Digikey
CA3140 Opamp | 6 | $3.82 | $22.92 | Digikey
Fast blow Fuse Kit (https://www.amazon.ca/Fast-Blow-Assorted-5x20mm-Professional-Electrical/dp/B07PDMFXYR) | 1 | $13.98 | $13.98 | Amazon
6pcs Solderable 1/2 Breadboard (https://www.amazon.ca/Cylewet-Solderable-Half-Sized-Breadboard-Arduino/dp/B07HDY1K2N?hvadid=208400857623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) | 1 | $16.99 | $16.99 | Amazon
RJ45 Jack/Breakout Board | 13 | $2.86 | $37.18 | Digikey
2N4424 NPN Transistor | 4 | $0.56 | $2.24 | Digikey
5*12 Pos terminal blocks | 1 | $10.50 | $10.50 | Amazon
50 ft 18awg blue wire | 1 | $21.31 | $21.31 | Amazon
RJ45 Screw Terminal | 1 | $12.99 | $12.99 | Amazon
22AWG Assorted Wire (https://www.aliexpress.com/item/32958017642.html) | 1 | $21.00 | $21.00 | Amazon
HC-05 Bluetooth serial device | 1 | $10.99 | $10.99 | Amazon
20ft 10AWG red/blk wire | 1 | $21.97 | $21.97 | Amazon
10 pair XT90 | 1 | $26.12 | $26.12 | Amazon
800pcs Assorted Heatshrink | 1 | $16.99 | $16.99 | Amazon
12V horn | 1 | $10.10 | $10.10 | Amazon
10 pair XT60 | 1 | $23.10 | $23.10 | Amazon
10ft 12 awg wire red/blk | 1 | $11.97 | $11.97 | Amazon
12V 500A Solenoid | 1 | $36.99 | $36.99 | Amazon
10' door stop foam tape | 2 | $10.82 | $21.64 | Amazon
18AWG Assorted Wire | 1 | $23.88 | $23.88 | Amazon
12/24VDC to 5V 10A converter | 1 | $22.99 | $22.99 | Amazon
8 Channel relay | 8 | $12.86 | $102.88 | Amazon
10x xt30 connectors | 1 | $11.19 | $11.19 | Amazon
Arduino Mega 16u2 interface | 2 | $10.60 | $21.20 | Banggood
Arduino Nano | 3 | $2.24 | $6.72 | Banggood
2x replacement turn signals | 1 | $13.80 | $13.80 | Banggood
Taillight | 1 | $11.92 | $11.92 | Banggood
Headlight | 1 | $40.21 | $40.21 | Banggood
65ft Cat5 | 2 | $6.89 | $13.78 | Banggood
50x RJ45 rubber boots | 1 | $7.60 | $7.60 | Banggood
50x RJ45 Plug | 1 | $4.52 | $4.52 | Banggood
4-pin CB connector pair | 8 | $2.31 | $18.48 | Banggood
RJ45 Screw Terminal Male | 2 | $5.89 | $11.78 | Banggood
Cat5 Crimp tool | 1 | $16.08 | $16.08 | Banggood
Subtotal of Bike Components |  |  | $1680.00
Subtotal of Capstone Components |  |  | $967.71
Grand Total |  |  | $2647.71

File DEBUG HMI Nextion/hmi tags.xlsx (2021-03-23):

objname | page id | id | type | vscope | Button? | description
 |  |  |  |  |  |  |  | PAGES
alarmView | 0 | 2 | text | local | Yes | Fault rotation screen | 50 | 0 | MAIN
vBat | 0 | 14 | text | local | no | vbat indicator float .0 | 10 | 1 | Alarms
currentDisplay | 0 | 15 | text | local | no | Current display in A float .00 | 10 | 2 | Status
powerDisplay | 0 | 16 | text | local | no | power display in W | 10
mAh | 0 | 17 | text | local | no | capacity draw in mAh | 10
FLTRST | 0 | 3 | Button | local | yes | fault reset
speedDisplay | 0 | 4 | text | local | no | speed in km/h | 10
inGearInd | 0 | 1 | text | local | no | blue D in drive, green N in neutral | 1
STAT | 0 | 5 | button | local | yes | go to status screen (page 2)
clock | 0 | 13 | text | local | no | display buffered time from arduino | 10
voltBar | 0 | 9 | bar | local | no | progress bar volts
currBar | 0 | 10 | bar | local | no | progress bar current capacity
powerBar | 0 | 11 | bar | local | no | power bar power capacity
alarm0 | 1 | 1 | text | local | no | Fault Display | 50
alarm1 | 1 | 5 | text | local | no | Fault Display | 50
alarm2 | 1 | 6 | text | local | no | Fault Display | 50
alarm3 | 1 | 7 | text | local | no | Fault Display | 50
alarm4 | 1 | 8 | text | local | no | Fault Display | 50
alarm5 | 1 | 9 | text | local | no | Fault Display | 50
alarm6 | 1 | 10 | text | local | no | Fault Display | 50
alarm7 | 1 | 11 | text | local | no | Fault Display | 50
alarm8 | 1 | 12 | text | local | no | Fault Display | 50
alarm9 | 1 | 13 | text | local | no | Fault Display | 50
FLTRST | 1 | 4 | button | local | yes | reset faults
STAT | 1 | 3 | button | local | yes | go to status screen (page 2)
MAIN | 1 | 2 | button | local | yes | go to main screen (page 0)
alarmView | 2 | 2 | text | local | yes | go to alarm screen (page 1)
FLTRST | 2 | 3 | button | local | yes | reset faults
vBat | 2 | 16 | text | local | no | view total battery
currentDisplay | 2 | 17 | text | local | no | view current draw in A
powerDisplay | 2 | 18 | text | local | no | view power draw in W
mAh | 2 | 19 | text | local | no | current draw in mAh
speedDisplay | 2 | 4 | text | local | no | speed in km/h
inGearInd | 2 | 15 | text | local | no | ingear ind
MAIN | 2 | 1 | button | local | yes | go to main screen
cell1v | 2 | 22 | text | local | no | cell volts .0 precision
cell2v | 2 | 23 | text | local | no | cell volts .0 precision
cell3v | 2 | 24 | text | local | no | cell volts .0 precision
cell4v | 2 | 25 | text | local | no | cell volts .0 precision

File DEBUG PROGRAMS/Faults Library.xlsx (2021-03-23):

faultFlags[32] | Fault bit | Level of fault | String displayed | FltRst? | Done
0 | anyFaultsDetected | 3 | <no display, just a generic bit to say anything detected> | No
1 | allConnectionsOK | 1 | Lost connection to an essential component! | No
2 | watchdogFlag | 1 | Processor cycle overtime! | Yes
3 | optoPowerLost | 1 | Optocoupler board power loss detected | Yes
4 | handlebarPowerLeftFault | 1 | Left handlebar lost connection to controller! | Yes
5 | handlebarPowerRightFault | 1 | Right handlebar lost connection to controller! | Yes
6 | throttleOutOfBoundsFlag | 2 | Throttle reading out of bounds detected! | Yes
7 | throttleOutOfBounds | 1 | Throttle reading out of bounds detected! | No
8 | cellOneLow | 2 | Cell 1 Low! | No
9 | cellTwoLow | 2 | Cell 2 Low! | No
10 | cellThreeLow | 2 | Cell 3 Low! | No
11 | cellFourLow | 2 | Cell 4 Low! | No
12 | anyLevel2FaultDetected | 2 | At least one warning detected! | No
13 | motorContactorFault | 1 | Problem detected with the motor contactor! | Yes
14 | trackerBitsOverLoad | 1 | Function tracking bits overloaded; please restart the processor! | Yes
15 | thlNotIdleWhenReq | 3 | Throttle must be at idle to enter gear | Yes
16 | controlOvercurrentFlag | 2 | High current detected at 12V shunt (>12A) | Yes
17 | anyLevel1FaultDetected | 1 | Critical fault detected! | No
18 | unableToLoadEEPROM | 2 | EEPROM values unavailable; cannot record odometer | Yes
19 | anyCellCritical | 1 | Battery cell at critical level; please stop riding | Yes
20 | throttleFeedbackFault | 1 | Throttle out to ESC not what was expected; please check wiring | Yes
21
22
23 | unexpectedTimerFault | 1 | Unexpected timerTracker value detected!! | Yes
24 | unexpectedONSFault | 1 | ONSTracker different than expected, check code! | Yes
25 | auxPowerFault | 2 | Aux power is off; IO will not work correctly | No
26 | hmiOvertimeFault | 2 | HMI overtime, disabling Nextion | Yes
27
28
29
30
31

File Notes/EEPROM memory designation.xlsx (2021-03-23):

Address | Name | Type | Size
0..3 | odometer | Float | 4
4..7 | odometerTune | float | 4
8..11 | vBatTune | float | 4
12..15 | smallShuntReadTune | float | 4
16..19 | temperatureTune | float | 4
20..23 | largeShuntReadTune | float | 4

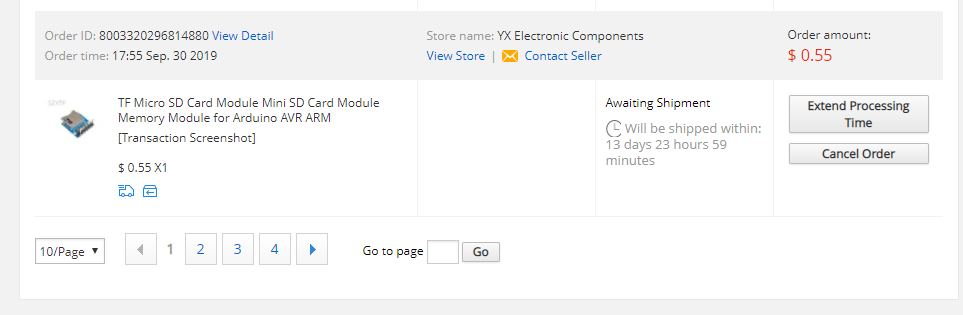
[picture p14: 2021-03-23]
Receipts/order page 4.PNG

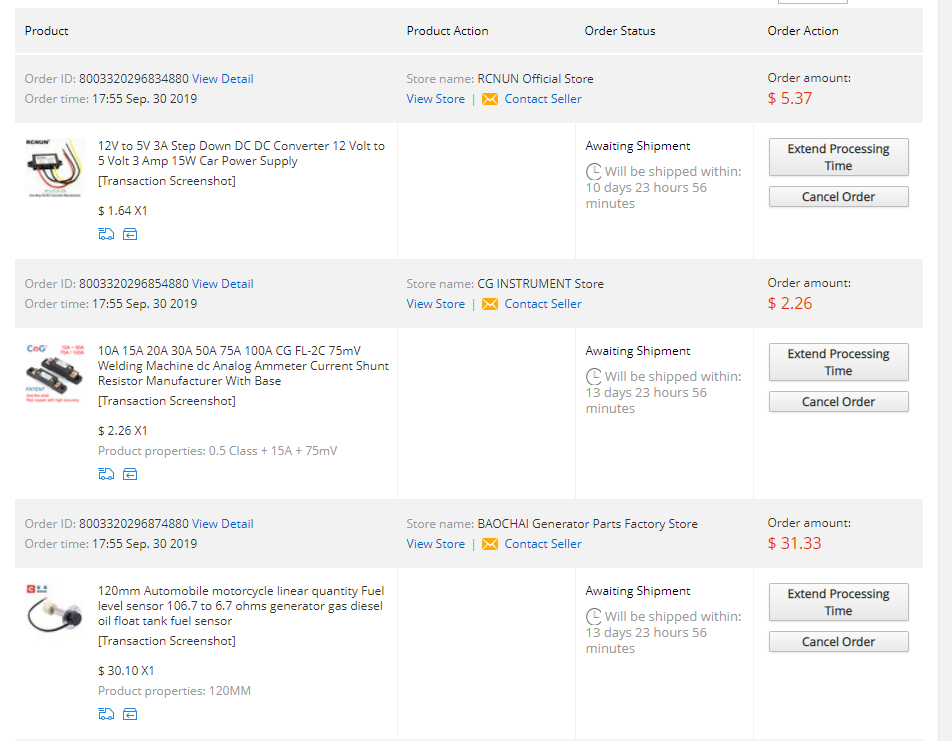
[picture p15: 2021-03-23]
Receipts/order page 5.PNG

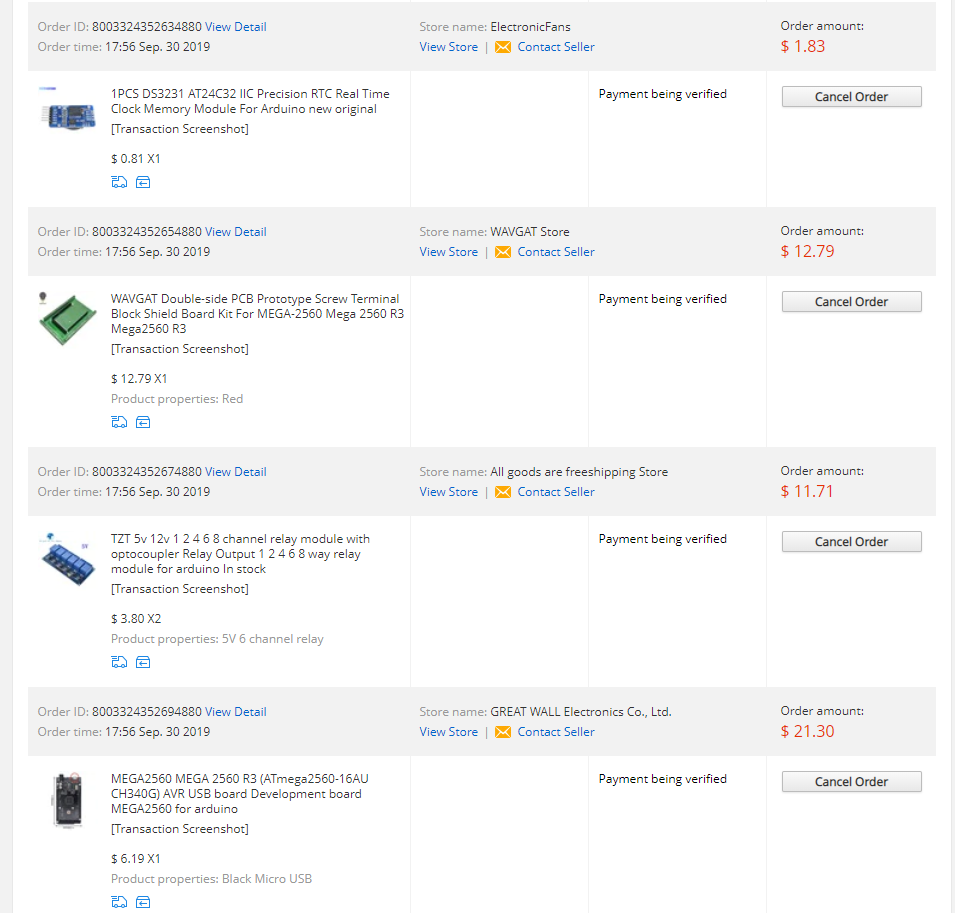
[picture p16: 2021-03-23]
Receipts/order page 2.PNG

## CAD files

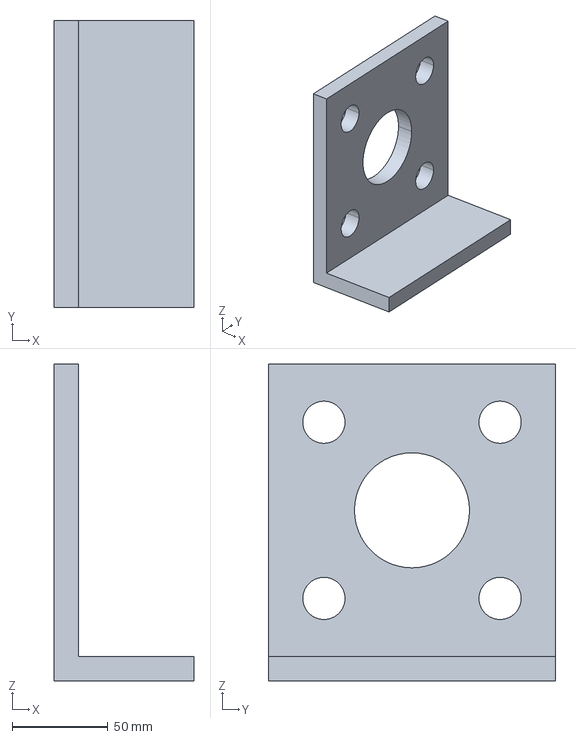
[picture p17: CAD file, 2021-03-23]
Documentation/Mechanical/Cole Assy.stp
72.9 x 150.0 x 165.4 mm

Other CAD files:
Documentation/MEGA PINOUT.dwg
Documentation/RH PANEL LAYOUT.dwg
Documentation/LH PANEL LAYOUT.dwg
Documentation/OPTO BOARD.dwg
Documentation/CENTER PANEL LAYOUT.dwg
Documentation/FRONT PANEL LAYOUT.dwg
Documentation/Designed Boards.dwg
Documentation/HANDLEBAR PINOUT.dwg
Documentation/MOTOR-CONTROLLER PANEL LAYOUT.dwg
Documentation/ETHERNET SCREW TERMINAL.dwg
Documentation/Archive/PANEL LAYOUTS.dwg
Documentation/Archive/Designed Boards Rev 1.dwg
Documentation/Mechanical/Cole Assy.CATProduct
Documentation/Mechanical/Motor Bracket.CATPart
Documentation/Mechanical/motor bolt circle.CATPart
Documentation/Mechanical/sprocket.CATPart

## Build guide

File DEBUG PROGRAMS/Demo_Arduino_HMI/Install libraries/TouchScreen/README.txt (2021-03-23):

This is the 4-wire resistive touch screen firmware for Arduino. Works with all Arduinos and the Mega

To install, click DOWNLOAD SOURCE in the top right corner, and rename the uncompressed folder "TouchScreen". See our tutorial at http://www.ladyada.net/library/arduino/libraries.html on Arduino Library installation

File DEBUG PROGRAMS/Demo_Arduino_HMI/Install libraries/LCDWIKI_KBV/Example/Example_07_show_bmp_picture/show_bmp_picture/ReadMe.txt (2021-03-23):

ReadMe:
"ShowBMP"example need to read BMP files from SDcard.
so, firstly,you should format your SD-card into fat16 or fat32.
then copy the flower.bmp,RedRose.bmp,tiger.bmp,tree.bmp into your SD-card.

Attention:
This Example only support the Arduino UNO board,not support the Mega2560,Because they use different SPI bus.

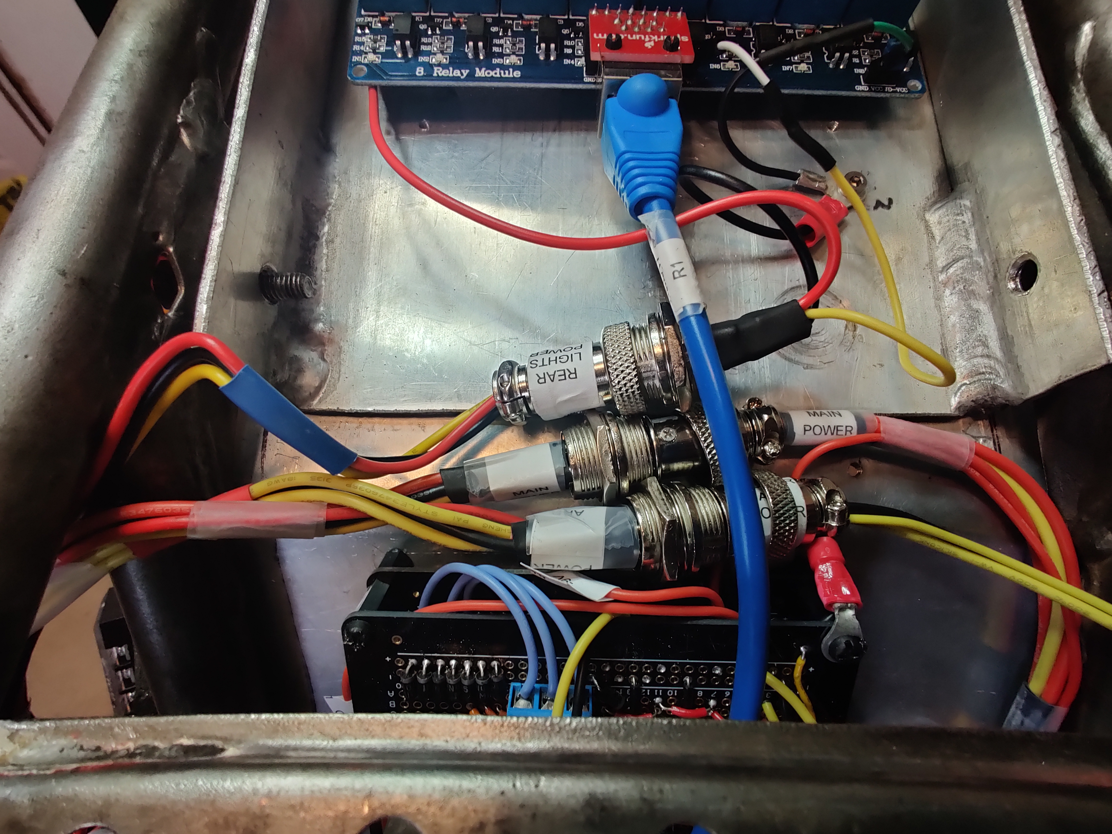
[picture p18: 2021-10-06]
Cole Fuerth Project Photo Repository/Wiring/Main CB Connectors.jpg

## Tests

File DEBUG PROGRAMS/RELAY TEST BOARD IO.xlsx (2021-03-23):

Arduino Test Pilot I/O
Arduino Pin |  | Description | Purpose
D | 0 | LED 0 | throttle int bit 7
D | 1 | LED 1 | throttle int bit 6
D | 2 | LED 2 | throttle int bit 5
D | 3 | LED 3 | throttle int bit 4
D | 4 | LED 4 | throttle int bit 3
D | 5 | LED 5 | throttle int bit 2
D | 6 | LED 6 | throttle int bit 1
D | 7 | LED 7 | throttle int bit 0
D | 8 | motor | Motor PWM Out
D | 9
D | 10 | TOUCH 1 | Left Turn
D | 11 | TOUCH 2 | Right Turn
D | 12 | TOUCH 3 | Hazards
D | 13 | TOUCH 4 | HighBeams
D | 17 | PB 1 | In/Out of Gear
D | 21 | LAMP 1 | In/Out of Gear
D | 22 | RELAY 1 | RL Turn
D | 23 | RELAY 2 | RR Turn
D | 24 | RELAY 3 | FL Turn
D | 25 | RELAY 4 | FR Turn
D | 26 | RELAY 5 | Low Beams
D | 27 | RELAY 6 | High Beams
A | 0 | POT 1 | Throttle Input

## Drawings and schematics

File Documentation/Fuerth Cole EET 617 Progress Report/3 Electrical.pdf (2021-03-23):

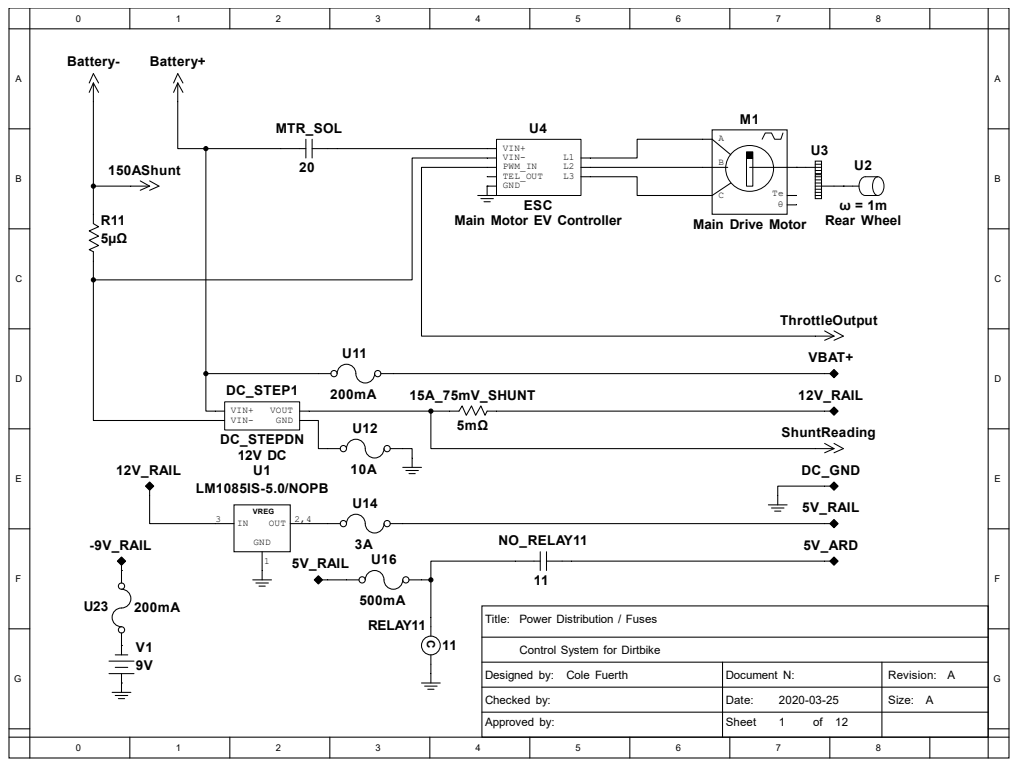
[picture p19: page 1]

Main Motor EV Controller

Control System for Dirtbike
Designed by:
Checked by:
Approved by:

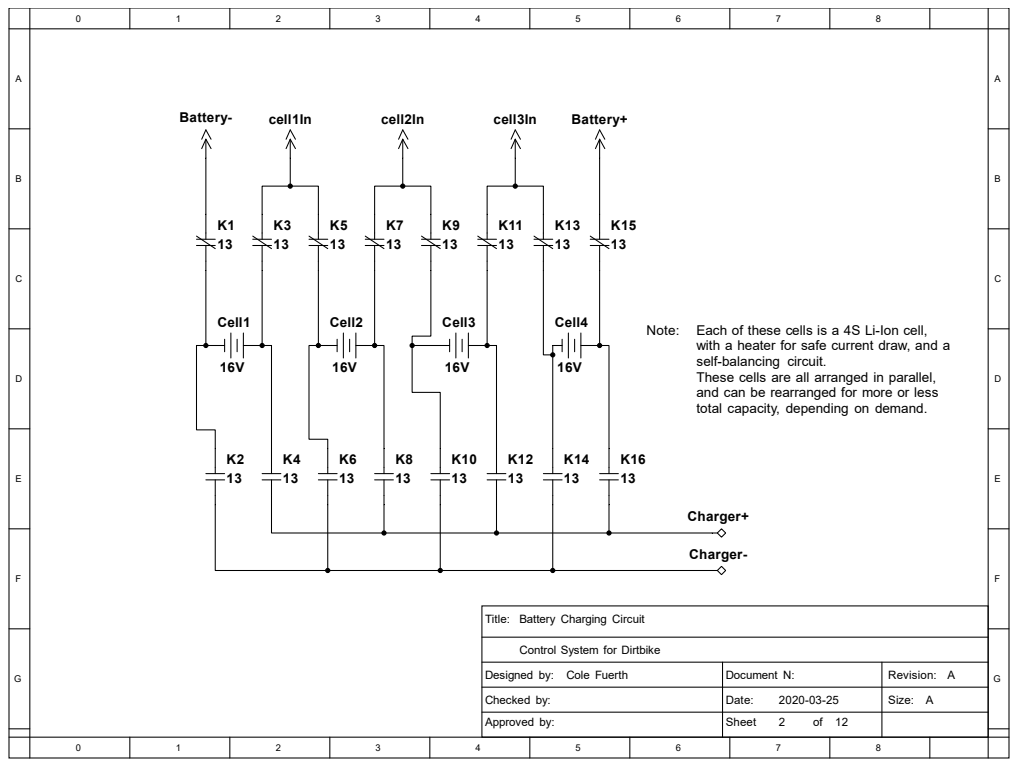
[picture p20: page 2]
Title:; Document N:; Date:; Sheet; Revision:; Size:; Cole Fuerth; Cell1; Cell4; Cell2; Cell3; Charger+; Charger-; Battery-; cell1In; cell2In; cell3In; Battery+

Note: Each of these cells is a 4S Li-Ion cell,

with a heater for safe current draw, and a
self-balancing circuit.
These cells are all arranged in parallel,
and can be rearranged for more or less
total capacity, depending on demand.

Battery Charging Circuit

Control System for Dirtbike
Designed by:
Checked by:
Approved by:

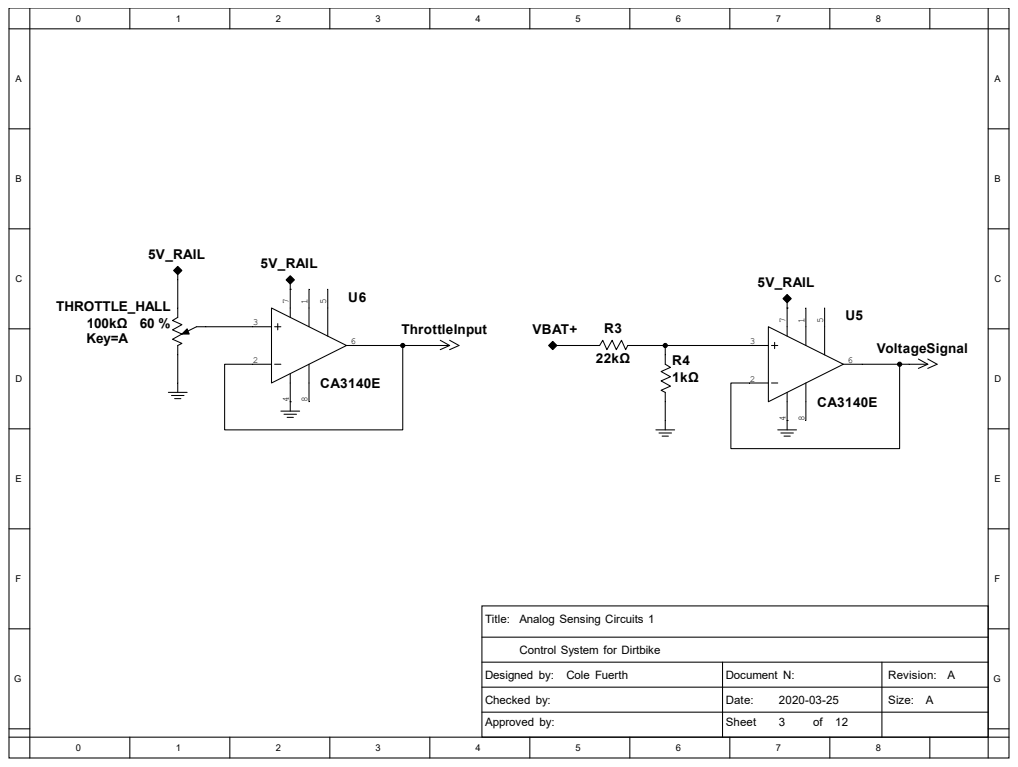
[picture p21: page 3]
Title:; Document N:; Date:; Sheet; Revision:; Size:; Cole Fuerth; VBAT+; 5V_RAIL; VoltageSignal; THROTTLE_HALL 100kΩ Key=A; ThrottleInput

Analog Sensing Circuits 1

Control System for Dirtbike
Designed by:
Checked by:
Approved by:

2 4 7

2 4 7

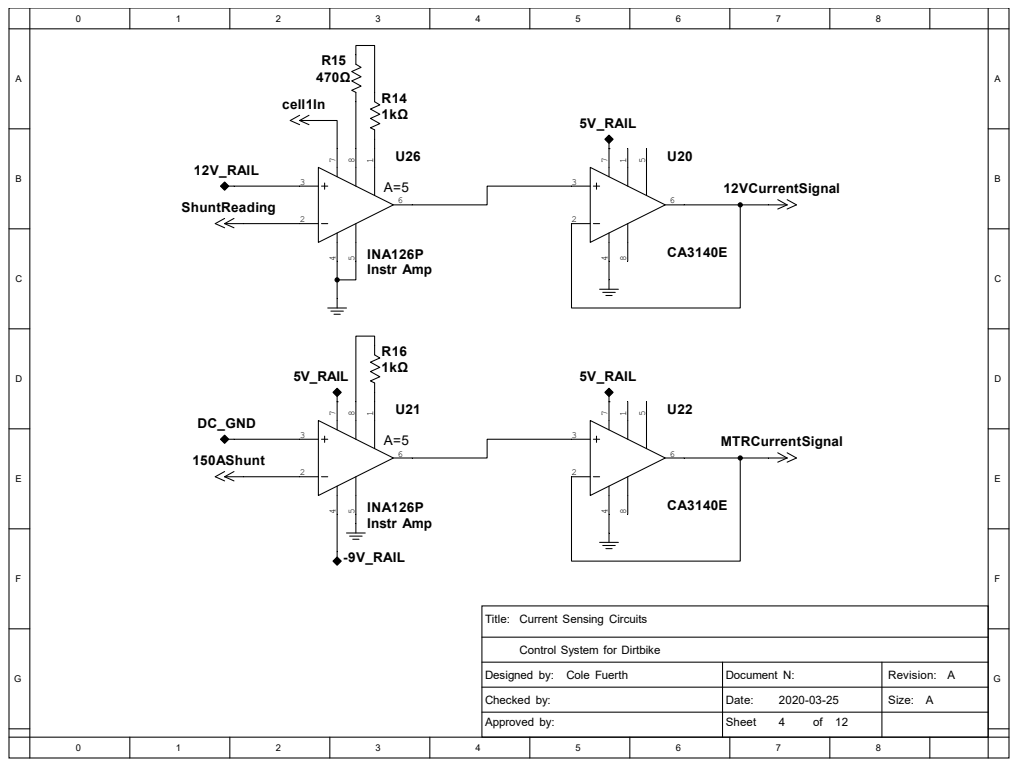
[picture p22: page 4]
Title:; Document N:; Date:; Sheet; Revision:; Size:; Cole Fuerth; ShuntReading; 12V_RAIL; 12VCurrentSignal; INA126P Instr Amp; 5V_RAIL; 150AShunt; MTRCurrentSignal; cell1In; -9V_RAIL; DC_GND

Current Sensing Circuits

Control System for Dirtbike
Designed by:
Checked by:
Approved by:

2 4 7

2 4 7

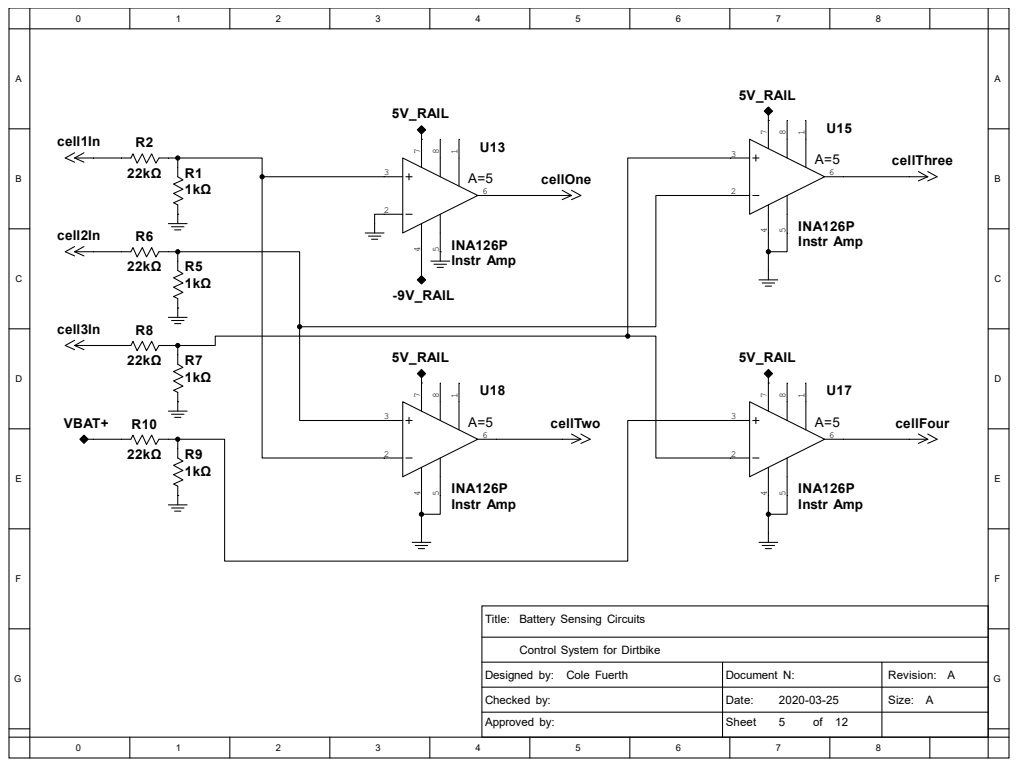
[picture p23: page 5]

Control System for Dirtbike
Designed by:
Checked by:
Approved by:

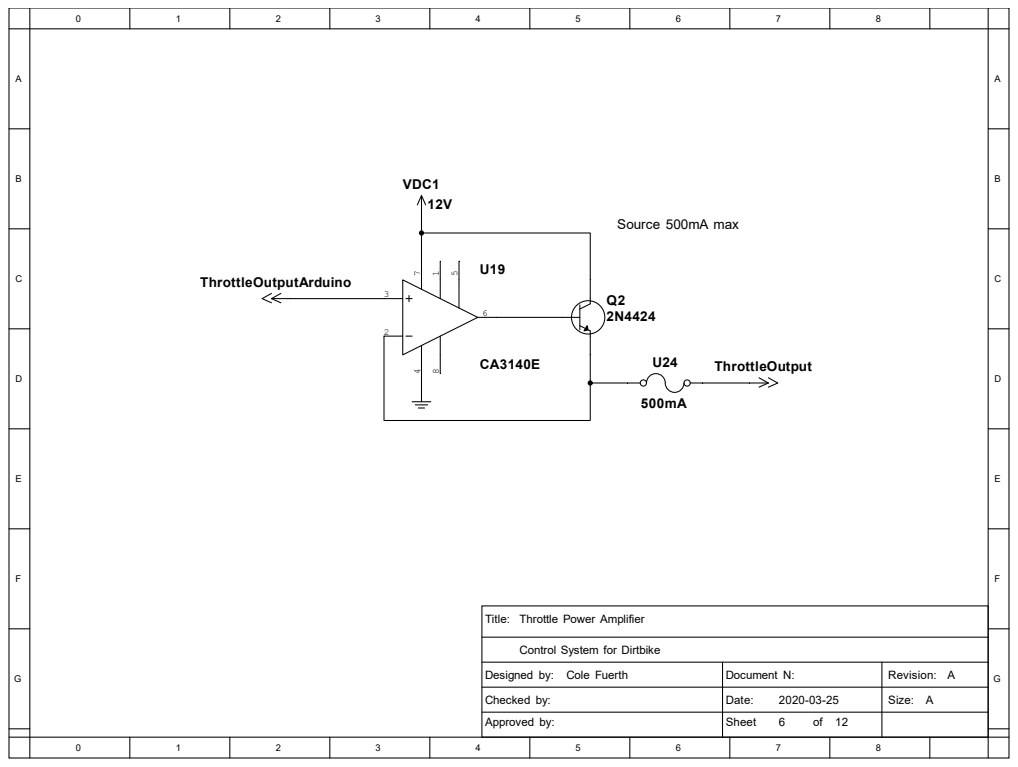
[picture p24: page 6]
VDC1 12V; ThrottleOutputArduino; ThrottleOutput; Title:; Document N:; Date:; Sheet; Revision:; Size:; Cole Fuerth; Source 500mA max

Throttle Power Amplifier

Control System for Dirtbike
Designed by:
Checked by:
Approved by:

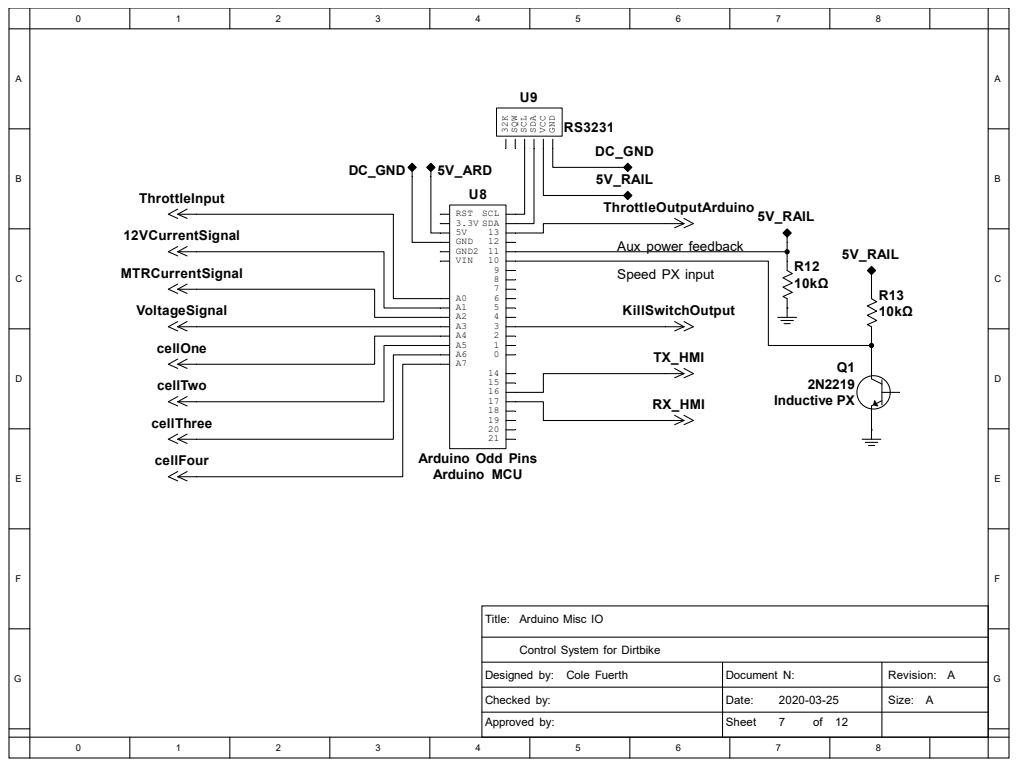
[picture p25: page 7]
Title:; Document N:; Date:; Sheet; Revision:; Size:; Cole Fuerth; 3.3V 5V GND GND2 VIN; SDA; SCL; RST; ThrottleInput; 12VCurrentSignal; VoltageSignal; TX_HMI; RX_HMI; ThrottleOutputArduino; 5V_RAIL; DC_GND; MTRCurrentSignal; cellOne; cellTwo; cellFour; cellThree; Q1 2N2219 Inductive PX; KillSwitchOutput; 5V_ARD

U9 32K SQW SCL SDA VCC GND RS3231

Aux power feedback
Speed PX input

Arduino Odd Pins
Arduino MCU

Arduino Misc IO

Control System for Dirtbike
Designed by:
Checked by:
Approved by:

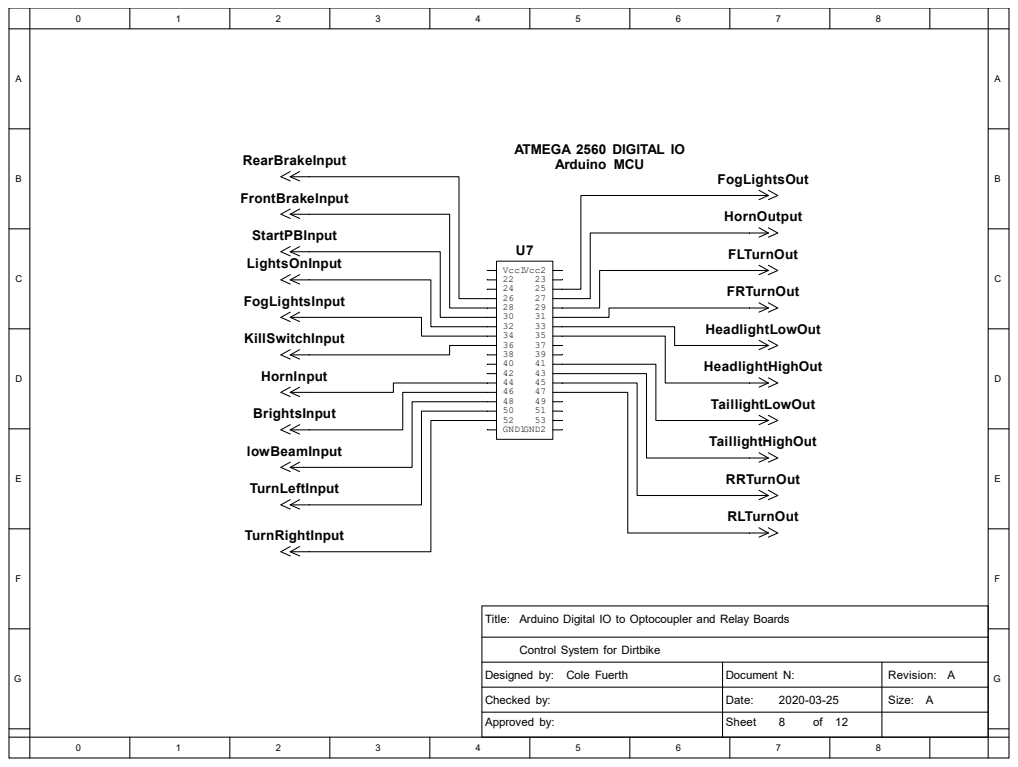
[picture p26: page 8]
Vcc1 22 24 26 28 30 32 34 36 38 40 42 44 46 48 50 52 GND1GND2; Vcc2; HeadlightLowOut; TaillightLowOut; FogLightsOut; FRTurnOut; RRTurnOut; KillSwitchInput; FogLightsInput; StartPBInput; lowBeamInput; TurnRightInput; HeadlightHighOut; TaillightHighOut; LightsOnInput; BrightsInput; TurnLeftInput; HornInput; HornOutput; Title:; Document N:; Date:; Sheet; Revision:; Size:; Cole Fuerth; FrontBrakeInput; FLTurnOut; RLTurnOut; RearBrakeInput

ATMEGA 2560 DIGITAL IO
Arduino MCU

Arduino Digital IO to Optocoupler and Relay Boards

Control System for Dirtbike
Designed by:
Checked by:
Approved by:

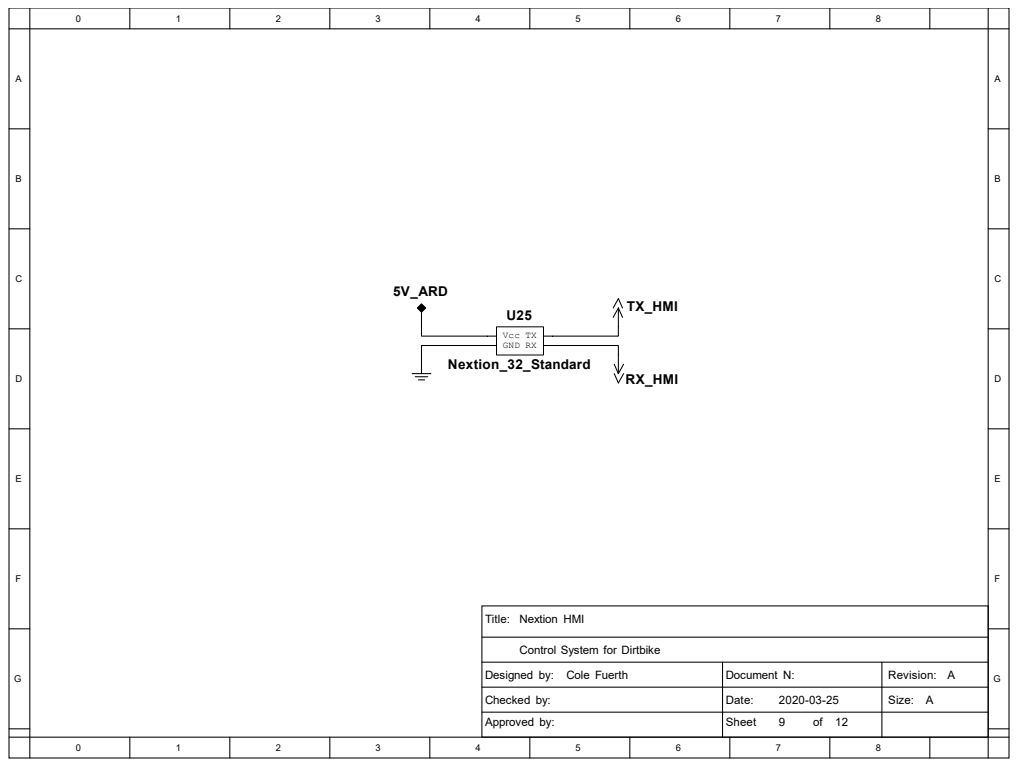
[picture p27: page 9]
Title:; Document N:; Date:; Sheet; Revision:; Size:; Nextion HMI; Cole Fuerth; TX_HMI; RX_HMI; 5V_ARD; Nextion_32_Standard; Vcc GND RX

Control System for Dirtbike
Designed by:
Checked by:
Approved by:

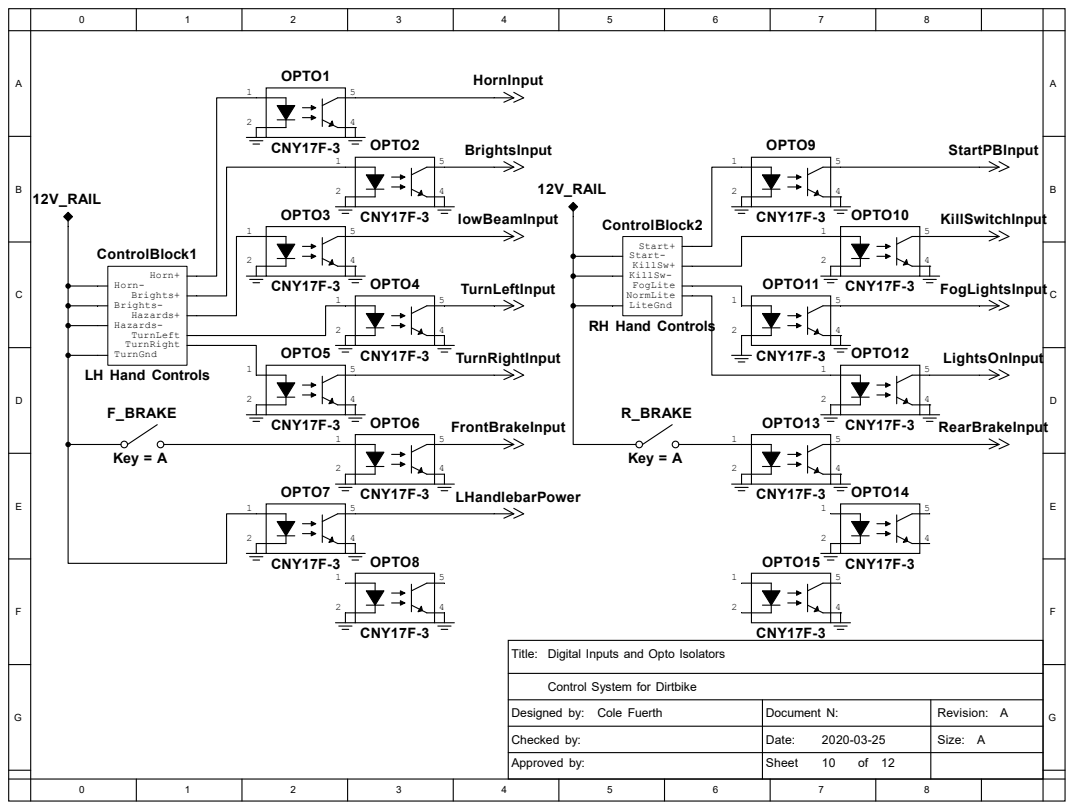
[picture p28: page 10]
Title:; Document N:; Date:; Sheet; Revision:; Size:; Cole Fuerth; ControlBlock1; LH Hand Controls; Horn+; Horn- Brights+ Brights- Hazards+ Hazards- TurnLeft TurnRight TurnGnd; OPTO3; CNY17F-3; OPTO4; OPTO1; OPTO2; OPTO5; OPTO6; OPTO7; OPTO8; 12V_RAIL; HornInput; BrightsInput; lowBeamInput; TurnLeftInput; TurnRightInput; OPTO11; OPTO12; OPTO9; OPTO10; ControlBlock2; RH Hand Controls; Start+ Start- KillSw+ KillSw- FogLite NormLite LiteGnd; StartPBInput; KillSwitchInput; FogLightsInput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

Digital Inputs and Opto Isolators

Control System for Dirtbike
Designed by:
Checked by:
Approved by:

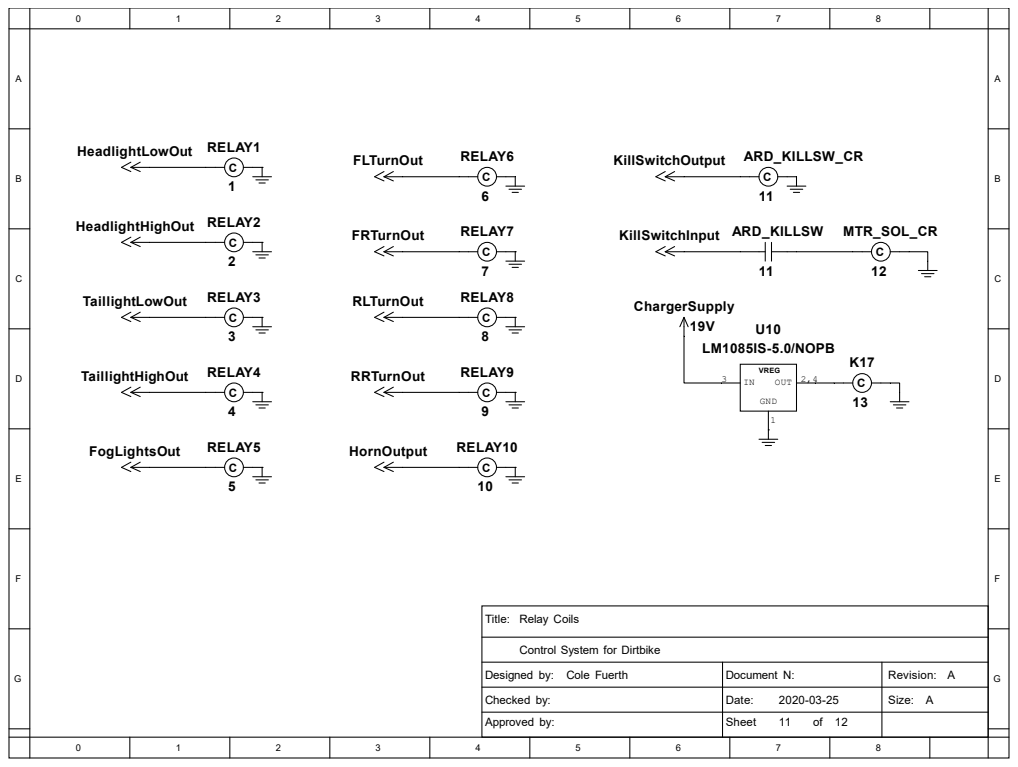
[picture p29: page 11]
Title:; Document N:; Date:; Sheet; Revision:; Size:; Relay Coils; Cole Fuerth; RELAY1; RELAY2; RELAY3; RELAY4; RELAY6; RELAY7; RELAY8; RELAY9; RELAY5; HeadlightLowOut; TaillightLowOut; FogLightsOut; FRTurnOut; RRTurnOut; HeadlightHighOut; TaillightHighOut; FLTurnOut; RLTurnOut; RELAY10; HornOutput; KillSwitchInput; KillSwitchOutput; ARD_KILLSW_CR; MTR_SOL_CR; ChargerSupply; LM1085IS-5.0/NOPB; VREG; GND; OUT 2,4; ARD_KILLSW

Control System for Dirtbike
Designed by:
Checked by:
Approved by:

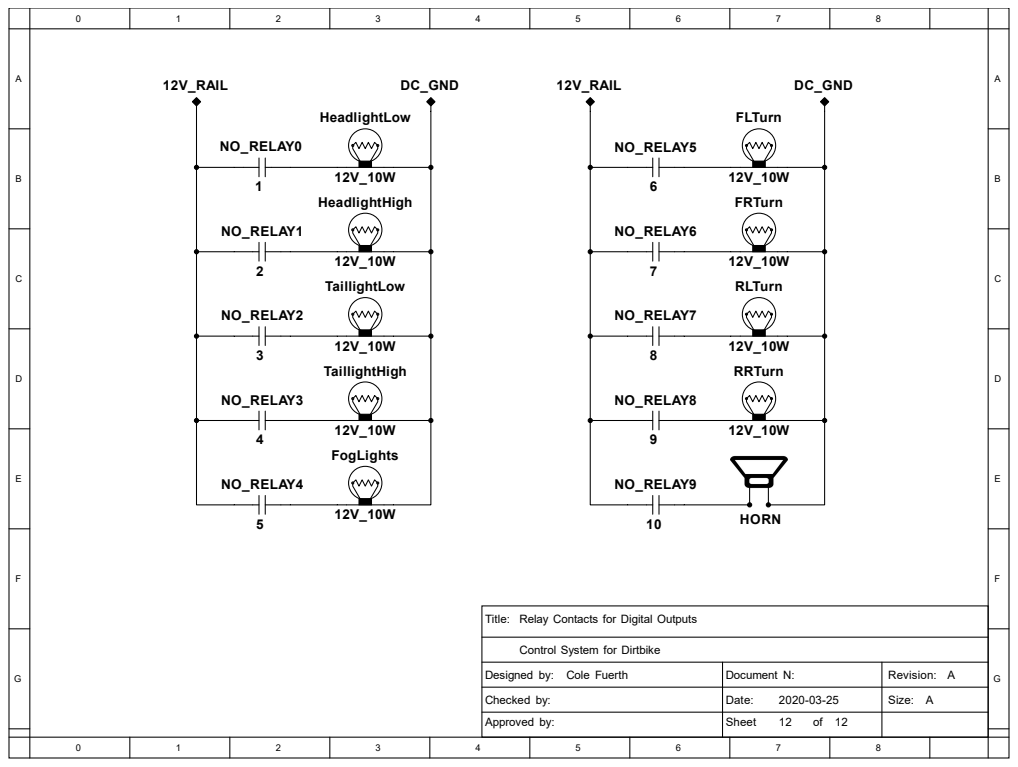
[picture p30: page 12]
Title:; Document N:; Date:; Sheet; Revision:; Size:; Cole Fuerth; NO_RELAY0; NO_RELAY1; NO_RELAY3; NO_RELAY2; NO_RELAY4; NO_RELAY5; NO_RELAY6; NO_RELAY7; NO_RELAY8; 12V_RAIL; DC_GND; HeadlightLow; HeadlightHigh; TaillightLow; TaillightHigh; FogLights; FLTurn; FRTurn; RLTurn; RRTurn; NO_RELAY9; 10 HORN

Relay Contacts for Digital Outputs

Control System for Dirtbike
Designed by:
Checked by:
Approved by:

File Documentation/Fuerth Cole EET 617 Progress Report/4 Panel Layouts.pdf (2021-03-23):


ST. CLAIR COLLEGE DRN BY CLASS TITLE DATE SCALE C.C.F 001 MAR'20 FULL LH PANEL LAYOUT 1+ 1- 2+ 2- 3+ 3- 4+ 4- 5+ 5- 6+ 6- 7+ 7- 8+ 8- GND VCC 01 02 03 04 05 06 07 08 OP WER MEGA2560 RESET ICSP ATMEL MEGA2560 22242628303234363840424446485052 A8A9A10 A11 A12 A13 A14 A15 A7A6A5A4A3A2A1A0VIN GND 5V3.3V RESET 5V 131211 1098765432101415161718192021 SCL SDA AREF GND RX0 TX0 RX3 TX3 RX2 TX2 RX1 TX1 SCL SDAPWM DIGITAL ANALOG IN POWER COM UNICATION CH340 PRODUCED BY AN AUTODESK STUDENT VERSION PRODUCED BY AN AUTODESK STUDENT VERSION

# PRODUCED BY AN AUTODESK STUDENT VERSION PRODUCED BY AN AUTODESK STUDENT VERSION

FUSED; 5VDC; 0VDC; 12VDC SPARE SMALL

ST. CLAIR COLLEGE DRN BY CLASS TITLE DATE SCALE C.C.F 001 MAR'20 FULL RH PANEL LAYOUT -9V FUSE 5VDC RAIL ARDUINO POWER SPARE 12VDC RAIL 3A500mA 10A

# PRODUCED BY AN AUTODESK STUDENT VERSION PRODUCED BY AN AUTODESK STUDENT VERSION

INA126P Cell 1 CELL1 CELL3 123; +IN GND; Vcc OUT; CELL2 CELL4 GND; INA126P Cell 3 123 5 4 678 123 5 4 678; INA126P Cell 2; INA126P Cell 4 ETH 12345678

ST. CLAIR COLLEGE DRN BY CLASS TITLE DATE SCALE C.C.F 001 MAR'20 FULL CENTER PANEL LAYOUT ETH ETH SCL SDA VCC GND DS3231 RTC CA3140 Throttle Buffer In 12345678 87654321 SCL SDA TH-I RXTXVCC GND GND VCC TXRXTH-I 1234 5876 To ARD To HMI Pin 6 +IN GND Vcc OUT CA3140 Throttle Buffer Out 1234 8765 +IN GND 12V OUT TH-O 12V Rail THR OUT GND 2N4424 Throttle Power Amp Base Collector Emitter vBat Buffer 12V THR OUT Pin 6

PRODUCED BY AN AUTODESK STUDENT VERSION

Vbat buf'd signal 12v shunt buf'd signal Mtr Shunt buf'd signal 50V-100V to 12V DC-DC MTR SHUNT 12V SHUNT -9 VDC THL OUT 5V RAIL 0 VDC 12 VDC RAIL CELL 4 / VBAT CELL 3 CELL 2 CELL 1 0 VDC / GND

Vcc OUT GND

vBat Mcurr 12vcurr Cell1 Cell2 Cell3 Cell4 To Arduino ANLG

# PRODUCED BY AN AUTODESK STUDENT VERSION PRODUCED BY AN AUTODESK STUDENT VERSION


ST. CLAIR COLLEGE DRN BY CLASS TITLE DATE SCALE C.C.F 001 MAR'20 FULL FRONT PANEL LAYOUT ETH 12345678 To ARD-F2 F 2 SPE D PX 5 VDC RA LI 12 VDC RA LI GND H GI H BEAM LOW BEAM GND TURN RIGHT TURN LEFT HORN GND FOG


ST. CLAIR COLLEGE DRN BY CLASS TITLE DATE SCALE C.C.F 001 MAR'20 FULL MOTOR-CONTROLLER INTERFACE PANEL LAYOUT ETH 12345678 To ARD M- 3 05 M 3 mV 150A MTR SHUNT MTR CONTACTOR SOLENO DI PRODUCED BY AN AUTODESK STUDENT VERSION PRODUCED BY AN AUTODESK STUDENT VERSION

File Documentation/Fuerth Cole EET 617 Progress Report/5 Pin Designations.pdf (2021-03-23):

# PRODUCED BY AN AUTODESK STUDENT VERSION PRODUCED BY AN AUTODESK STUDENT VERSION

3.3V RESET; SCL SDA; AREF GND; RX0 TX0 RX3 TX3 RX2 TX2 RX1 TX1 SCL SDAPWM; ETH 0 PIN 8; 5V RAIL FEEDBACK; ARD POWER

ST. CLAIR COLLEGE DRN BY CLASS TITLE DATE SCALE C.C.F 001 JAN'20 FULL ATMEGA 2560 PIN LAYOUT MEGA2560 RESET ICSP ATMEL MEGA2560 ETH 1 RELAY BOARD 1 22242628303234363840424446485052 A8A9A10 A11 A12 A13 A14 A15 A7A6A5A4A3A2A1A0VIN GND GND

ETH 4 RELAY BOARD 3 OPTO BOARD 2 OPTO BOARD 1

ETH 0 PIN 7 ETH 0 PIN 6 ETH 0 PIN 5 ETH 0 PIN 3 ETH 0 PIN 4 COMMUNICATION CH340 ETH 2 RELAY BOARD 2 ETH 3 ANLALOG STACK

PRODUCED BY AN AUTODESK STUDENT VERSION

DIGITAL ANALOG IN POWER

# ETH

# ETH GND

VCC; SDA; SCL DS3231 RTC; shunt buffer 12345678; 12V Shunt In; GND; TXRX; TH-I SDA; SCL GND; VCC TXRX; To ARD; To HMI; ST. CLAIR COLLEGE DRN BY CLASS TITLE DATE SCALE C.C.F 001 FEB'20; FULL DESIGNED BOARDS STACK; +IN GND; Vcc OUT; CA3140 Throttle Buffer Out 1234; 5678 +IN GND; 12V OUT; INA126P Cell 1; CELL1 CELL3; -IN +IN GND; INA126P Cell 3; INA126P Cell 2; INA126P Cell 4; ETH; CA3140 vBat buffer; INA126P; 12V Shunt; Vbat out 12v shunt out 1234; 12V +IN GND; +16V OUT; INA126P MTR; shunt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

PRODUCED BY AN AUTODESK STUDENT VERSION

vBat Mcurr 12vcurr Cell1 Cell2 Cell3 Cell4 To Arduino ANLG
CELL2 CELL4 GND

Vbat buf'd signal

Mtr Shunt buf'd signal

12v shunt buf'd signal

Vcc OUT GND

Pin 6 +IN GND

Vcc OUT
CA3140 Throttle Buffer In

THR OUT Pin 6

12V Rail THR OUT GND

2N4424 Throttle Power Amp

STACK ORDER,
BOTTOM TO TOP
Vcc OUT GND Mtr Shunt Mtr Shunt out Cell 1

12V shunt Vbat in +

5VGnd MTR Shunt In

12V Shunt Out
12V shunt buffer CA3140 MTR

5V Rail 12V Rail GND

# PRODUCED BY AN AUTODESK STUDENT VERSION PRODUCED BY AN AUTODESK STUDENT VERSION

POWER; LEFT TURN; LOW BEAM; HIGH BEAM; LIGHTS ON; FOG LIGHTS; START PB; FRONT BRAKE; REAR BRAKE; 38 HANDLEBAR POWER; FEEDBACK; HANDLEBAR POWER; CLUTCH SW

26 RIGHT HANDLEBAR OPTO BOARD 2 KILLSWITCH

ST. CLAIR COLLEGE DRN BY CLASS TITLE DATE SCALE C.C.F 001 FEB'20 FULL OPTO BOARD LAYOUT 1+ 1- 2+ 2- 3+ 3- 4+ 4- 5+ 5- 6+ 6- 7+ 7- 8+ 8- GND VCC 01 02 03 04 05 06 07 08

HORN 1+ 1- 2+ 2- 3+ 3- 4+ 4- 5+ 5- 6+ 6- 7+ 7- 8+ 8- GND VCC 01 02 03 04 05 06 07 08

PRODUCED BY AN AUTODESK STUDENT VERSION

44 LEFT HANDLEBAR OPTO BOARD 1 RIGHT TURN

flower YEL | GRN/YEL | PUR 1 RED 2 | 3 | 4 | 5 | 6 | 7 | 8 YEL/RED INPUT FROM RIGHT HANDLEBAR | 1.1039 ORA/RED 12V FEEDBACK SPEED PX | 12V FEEDBACK

# PRODUCED BY AN AUTODESK STUDENT VERSION PRODUCED BY AN AUTODESK STUDENT VERSION

flower BRN BLUE LBLUE GRN/BLK GRN/WHT 8; 1 INPUT FROM LEFT HANDLEBAR

ST. CLAIR COLLEGE DRN BY CLASS TITLE DATE SCALE C.C.F 001 FEB'20 FULL HANDLEBAR TO ETHERNET PINOUT

ST. CLAIR COLLEGE DRN BY CLASS TITLE DATE SCALE C.C.F 001 JAN'20 FULL HANDLEBAR PINOUT LH HAND CONTROLS RH HAND CONTROLS COLOR DESCRIPTION ORANGE TURN SIGNAL POWER GRN/WHT RIGHT TURN OUTPUT GRN/BLK LEFT TURN OUTPUT LBLUE OUTPUT TO LOWBEAM BLUE OUTPUT TO HIGH BEAM RED/WHT POWER FOR HI BEAM TRIGGER / DUAL LIGHT BRN HORN OUTPUT ORANGE/RED OUTPUT FROM CLUTCH SENSOR YELLOW/RED POWER FOR HI/LOW HEADLIGHT COLOR DESCRIPTION RED KILLSWITCH OUPUT YELLOW/RED LIGHTS ON OUTPUT YELLOW FOG LIGHTS OUTPUT BROWN/YELLOW POWER FOR START PB & KILLSWITCH GREEN/YELLOW START PB OUTPUT RED/WHITE POWER FOR BRAKE AND FOGLIGHT PURPLE FRONT BRAKE OUTPUT YEL YEL/RED GRN/YEL RED/WHT PUR RED BRN/YEL BRN YEL/RED GRN/BLK ORA LBLU RED/WHT GRN/WHT BLU ORA/RED

# PRODUCED BY AN AUTODESK STUDENT VERSION PRODUCED BY AN AUTODESK STUDENT VERSION


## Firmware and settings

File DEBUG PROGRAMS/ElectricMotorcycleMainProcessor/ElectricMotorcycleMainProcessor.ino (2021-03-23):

/*
 * ElectricMotorcycleMainProcessor.ino
 *
 * Created: 1/30/2020 1:39:49 PM
 * Author: cole_fuerth
 * Revision: Alpha 0.8.0	April 2020
 * Project: Control System for an Electric Motorcycle
 *
 * THIS SKETCH IS DESIGNED TO BE RUN ON AN ATMEGA 2560
 *
 */ 

/*
CHANGELOG
0.8.0	April 8, 2020
 - Added a fault for unrecognized serial message from Nextion

0.7.2	March 29, 2020
 - Nextion now only cycles through updates on the current screen in its cycle, so elements update much faster
 - voltsFromAnalogIn() was fixed, had a resolution problem and would only output integers
 - Nextion now sets its own baud to 115200 at startup
 - fixed some pointers not having an *asterisk
 - calibrated analog input values
 - analog boards were changed from 5v to 12v rails, and 5v safety diodes were added to protect the arduino
 - fixed current values on STAT page not updating
 - added throttle in and out bars to the stat page
 - added analog debugging settings
 - added fault debugging settings
 - fixed toggle logic
 - Fixed 'throttle out of bounds' fault always being on

0.7.1	March 27, 2020
 - Fixed button presses not being recognized
 - Some elements have become instant update rather than periodic
 - calibrated cell voltages
 - fixed speed logic

0.7.0	March 26, 2020
 - added a settings page to HMI with performance options
 - added indicators to main screen on HMI for brights and fog light indicators
 - added logic for updating HMI buffers to optimize HMI writing
 - added logic so that the 50hz update on elements only cycles through the current page, not all pages
 - added functionality so that the alarmView window changes colors based on the presence of faults
 - alarmView windows now flash red and gray when any critical faults are present
*/


/*  TODO
- Throttle to update on ISR instead of routinely
- Comment code more heavily
- Finish CLI logic
*/


#include <DS3231.h>
#include <Wire.h>
#include <Nextion.h>	// I have my own logic for this now
#include <Servo.h>
#include <Nextion.h>	

//define some color values for Nextion
#define BLACK   0x0000
#define BLUE    0x001F
#define RED     0xF800
#define ALRMRED	0xFC10
#define GREY	0x8410
#define GREEN   0x07E0
#define CYAN    0x07FF
#define LBLUE	0xAEBF
#define MAGENTA 0xF81F
#define YELLOW  0xFFE0
#define WHITE   0xFFFF
#define NEX_RET_EVENT_TOUCH_HEAD 0x65
#define nexSerial Serial2
#define dbSerial Serial

// function call memory bits available
	boolean oneShotBits[64];			// oneshot bits available for use for oneshot or toggle calls
										// BITS 32-63 ARE FOR FAULTS ONLY!!	
	
	uint8_t ONSTracker;
	// uint8_t debounceTracker;
	
	boolean timerInSession[32];		// for speed, so we only update timer timers when needed
	boolean timerMemory[sizeof(timerInSession)];			// make function calls smaller by remembering previous output state
	unsigned long timerTimers[sizeof(timerInSession)];	// debounce timers available for use
	uint8_t timerTracker;

// declare opto input arrays and input pins
	boolean opto1[8], opto2[8];
	const uint8_t opto1pins[8] = {52,50,48,46,44,42,40,38};
	const uint8_t opto2pins[8] = {36,34,32,30,28,26,24,22};
	
	boolean *killswitch				= opto2 ,
			*fogLightsIn			= opto2 + 1,
			*lightsOn				= opto2 + 2,
			*startPb				= opto2 + 3,
			*frontBrake				= opto2 + 4,
			*rearBrake				= opto2 + 5,
			*handlebarPowerRight	= opto2 + 6;
		
	boolean *rightTurnInput			= opto1 ,
			*leftTurnInput			= opto1 + 1,
			*lowBeamInput			= opto1 + 2,
			*highBeamInput			= opto1 + 3,
			*hornInput				= opto1 + 4,
			*clutchSwitchInput		= opto1 + 5,	
			*handlebarPowerLeft		= opto1 + 6,
			*optoPower				= opto1 + 7;
			
			
	boolean speedoPXInput;
	uint8_t speedoPXInputPin		= 10;
		
	
// declare analog inputs and pins
	const uint8_t auxPowerPin = 11;
	uint8_t analogInputTracker = 1;		// refresh one at a time, at 25Hz, except A0 is read at 25Hz on its own
	const uint8_t analogInputPins[8] = {PIN_A0,PIN_A9,PIN_A10,PIN_A11,PIN_A12,PIN_A13,PIN_A14,PIN_A15};
	int analogInputs[8];
	int	*throttleInput			= analogInputs,
		*currentDrawInput		= analogInputs + 1,
		*motorDrawInput			= analogInputs + 2,
		*vBatInput				= analogInputs + 3,
		*cellVoltageRawIn[4]	= { analogInputs+4,	analogInputs+5,
									analogInputs+6,analogInputs+7 };

// declare relay arrays and pointers
	boolean relayR1[6] = {0,0,0,0,0,0};	
	boolean relayF2[6] = {0,0,0,0,0,0};
	boolean relayM3[4] = {0,0,0,0};
	/*	note that the pins before and after each array are used for 
		power and ground for optocouplers on the relay inputs	*/
	const uint8_t relayR1Pins[6] = {41,43,45,47,49,51};
	const uint8_t relayF2Pins[6] = {35,33,31,29,27,25};
	const uint8_t relayM3Pins[4] = {3,4,5,6};	
		
	boolean *brakeLowOutput		= relayR1 + 0,
			*brakeHighOutput	= relayR1 + 1,
			*RRTurn				= relayR1 + 2,
			*RLTurn				= relayR1 + 3;
	
	boolean *highBeamsOut		= relayF2 + 0,
			*lowBeamsOut		= relayF2 + 1,
			*FRTurn				= relayF2 + 2, 
			*FLTurn				= relayF2 + 3,
			*hornOutput			= relayF2 + 4,
			*fogLightsOut		= relayF2 + 5;
			
	boolean *ESCSolenoid		= relayM3 + 0,
			*speedHighOut		= relayM3 + 1,
			*speedLowOut		= relayM3 + 2;
	
	
// Modes
	boolean inGear;
	boolean exitingGear = 0;

// clockRoutine Variables
	RTClib RTC;
	DateTime now;
	
// DriveSystem variables
	int throttlePercent;
	boolean killswOffSinceBoot = 0;
	boolean sportMode = 0,
			standardMode = 1,
			economyMode = 0;
	
// monitor system variables
	long last_cycleStart, totalDraw_mAh, last_analogCycleComplete, last_cycleStartus;
	int watchdog, longestCycle = 0, fastestCycle = 1000, watchdogus;
	int currentDrawMotorAmps, currentDrawShuntmA, speed, speedCount;
	int totalInGearSeconds = 0;
	float cellVolts[4], vBat;
	
	
// misc IO Variables, not done in the analog block
	int throttleOutput, pwmThrottleOutput;
	const uint8_t throttleOutputPin = 13;
	const uint8_t zzpwmOutputPin = 12;
	Servo zzpwmMotor;
	
	/*	NOT YET WORKING OR IMPLEMENTED
// SDCARD STUFF
	#include <SPI.h>
	#include <SD.h>
	File myFile;
	boolean SDActive, USBActive;
	uint8_t SDPin = 8;
	String logFileName;
	
// EEPROM values
	uint8_t	eepromAddress[1] = {0};
	float		eepromBuffer[1];
	float		*odometer		= eepromBuffer;*/
				
// FAULTS
	boolean faultFlags[32];
	boolean faultReset = 0;
	const uint8_t faultLevel[32] =		{
		0,	// 0
		1,	// 1
		1,	// 2
		1,	// 3
		1,	// 4
		1,	// 5
		3,	// 6
		1,	// 7
		2,	// 8
		2,	// 9
		2,	// 10
		2,	// 11
		0,	// 12
		1,	// 13
		1,	// 14
		3,	// 15
		2,	// 16
		1,	// 17
		2,	// 18
		1,	// 19
		1,	// 20
		0,	// 21
		0,	// 22
		1,	// 23
		1,	// 24
		2,	// 25
		2,	// 26
		0,	// 27
		0,	// 28
		0,	// 29
		0,	// 30
		0,	// 31
	};	// 1=critical	2=warning	3=status	0=unused
	const String faultMessages[32] =	{
		"",	// 0
		"Lost connection to an essential component!",	// 1
		"Processor cycle overtime!",	// 2
		"Opto board power loss detected",	// 3
		"Left handlebar lost connection to controller!",	// 4
		"Right handlebar lost connection to controller!",	// 5
		"Unrecognized serial msg received from HMI",	// 6
		"Throttle reading out of bounds detected!",	// 7
		"Cell 1 Low!",	// 8
		"Cell 2 Low!",	// 9
		"Cell 3 Low!",	// 10
		"Cell 4 Low!",	// 11
		"",	// 12
		"Problem detected with the motor contactor!",	// 13
		"Function tracking bits overloaded!",	// 14
		"Throttle must be at idle to enter gear",	// 15
		"High current detected at 12V shunt (>12A)",	// 16
		"Critical fault detected!",	// 17
		"EEPROM values unavailable; cannot record odometer",	// 18
		"Battery cell at critical level; please stop riding",	// 19		50 in length, for reference (faults cannot be longer than 50 in length
		"Throttle out feedback error",	// 20
		"",	// 21
		"",	// 22
		"Unexpected timerTracker value detected!!",	// 23
		"Unexpected ONSTracker value detected!!",	// 24
		"Aux power is off; IO will not work correctly. ",	// 25
		"HMI overtime, disabling Nextion",	// 26
		"",	// 27
		"",	// 28
		"",	// 29
		"",	// 30
		"", // 31
	};	
	int overTimeLength;	
	int expectedONS, expectedTimer;	
	int numberOfFaults;
	int numberScansPerSecond = 0;
	boolean anyFaultsDetected = 0;
	
	boolean *allConnectionsOK			= faultFlags + 1,
			*watchdogFlag				= faultFlags + 2,
			*optoPowerLost				= faultFlags + 3,
			*handlebarPowerLeftFault	= faultFlags + 4,
			*handlebarPowerRightFault	= faultFlags + 5,
			*nexReadUnrecognized		= faultFlags + 6,
			*throttleOutOfBounds		= faultFlags + 7,
			*cellOneLow					= faultFlags + 8,
			*cellTwoLow					= faultFlags + 9,
			*cellThreeLow				= faultFlags + 10,
			*cellFourLow				= faultFlags + 11,
			*motorContactorFault		= faultFlags + 13,
			*trackerBitsOverload		= faultFlags + 14,
			*thlNotIdleWhenReq			= faultFlags + 15,
			*controlOvercurrentFlag		= faultFlags + 16,
			*anyLevel1FaultDetected		= faultFlags + 17,
			*unableToLoadEEPROM			= faultFlags + 18,	
			*anyCellCritical			= faultFlags + 19,
			//*throttleFeedbackFault		= faultFlags + 20,
			*unexpectedTimer			= faultFlags + 23,
			*unexpectedONS				= faultFlags + 24,
			*auxPowerFault				= faultFlags + 25,
			*hmiOvertimeFault			= faultFlags + 26;


	// Nextion Variables for my functions
	int nextionPage = 0;		// current page of nextion to refresh; functionality being added later
	int activeFaultToDisplay = 0;
	int hmiElemToUpd = 0, thisSpot;
	boolean nextUpdate;
	String nexBufferMem[30];
	boolean nextionDelay = 0;
	uint8_t nexBytesRead[3];
			
	// DEBUG MEMORY ---------------------
	// settings that affect vehicle behavior
	boolean nextionEnabled				= 1;
	boolean contactorSafetiesActive		= 1;
	boolean faultsOnSerial				= 1;
	boolean debuggingActive				= 1;
	// settings that affect debug messages
	boolean debuggingHMIActive			= 0;
	boolean scanTimeDebugEnabled		= 0;
	boolean faultsDebuggingActive		= 0;
	boolean driveSystemDebuggingActive	= 0;
	boolean analogDebuggingActive		= 0;
	boolean speedDebugActive			= 0;
	boolean clockDebugActive			= 0;
	boolean motorControlDebugEnable		= 1;
	
	boolean firstScan					= 1;
	boolean auxPower;
	long debugTimer;
	int hmiOvertimeLength;


// MAIN PROGRAM
void setup()	
{
	zzpwmMotor.attach(zzpwmOutputPin);	// FOR PRESENTATION
	pinMode(9, OUTPUT);
	digitalWrite(9, LOW);	// 9 is the ground reference for the presentation motor
	
	int setupTime = millis();
	
	pinMode(auxPowerPin, INPUT);
	auxPower = digitalRead(auxPowerPin);
	
	// SETUP SERIAL FUNCTIONS
	if (debuggingActive) 
	{
		Serial.begin(115200);
		while (!TON(1, 50, 31) || !Serial) delay(10);	// wait 200ms for serial debugging to initialize
		//USBActive = Serial;
	}
	
	// setup Nextion
	if (nextionEnabled)
	{
		Serial.print("Initializing Nextion...");
		nexSerial.begin(115200);
		while (!TON(1, 50, 31) || !nexSerial) delay(10);
		if (nexSerial) Serial.println("Done.");
		else Serial.println("Failed.");
	}
	else Serial.println("Nextion is disabled in settings.");
	
	
	if (auxPower || clockDebugActive)
	{
		// setup RTC
		Serial.print("Wire.begin()...");
		Wire.begin();
		Serial.println("Done.");
		delay(10);
		Serial.print("initial read of DS3231...");
		now = RTC.now();				// update RTC value before starting Serial.println
		Serial.println("Done.");
		Serial.println("Current time is " + currentDate() + " " + currentTime());
		//logFileName = String(now.year()) + String(now.month()) + String(now.day()) + " " + String(now.hour()) + ":" + String(now.minute()) + ".txt";
		//if (SDActive) Serial.println("SDCard Serial.println now Active");
	}
	else Serial.println("No 5V aux power detected; skipping DS3231");
	
	
	// declare all pinModes
	
	if (debuggingActive) Serial.print("setting up opto inputs...");
	// opto inputs
	for (uint8_t i=0; i<sizeof(opto1pins); i++) pinMode(opto1pins[i], INPUT);
	for (uint8_t i=0; i<sizeof(opto2pins); i++) pinMode(opto2pins[i], INPUT);
	if (debuggingActive) Serial.println("Done.");
		
		
	if (debuggingActive) Serial.print("setting up relay outputs...");
	// relay outputs (R1 and R2):
	for (uint8_t i=0; i<sizeof(relayR1Pins); i++) pinMode(relayR1Pins[i], OUTPUT);
	for (uint8_t i=0; i<sizeof(relayF2Pins); i++) pinMode(relayF2Pins[i], OUTPUT);
	for (uint8_t i=0; i<sizeof(relayM3Pins); i++) pinMode(relayM3Pins[i], OUTPUT);
		
	// ensure the pulse to all relays so longer happens on startup
	for (uint8_t i=0; i<sizeof(relayR1); i++) digitalWrite(relayR1Pins[i], 1);
	for (uint8_t i=0; i<sizeof(relayF2); i++) digitalWrite(relayF2Pins[i], 1);
	for (uint8_t i=0; i<sizeof(relayM3); i++) digitalWrite(relayM3Pins[i], 1);
			
	// 5v/gnd constant pins for relay on-board optocouplers
	if (auxPower){
		// relay 1 power/gnd (front)
		pinMode(23, OUTPUT);
		digitalWrite(23, HIGH);
		pinMode(37, OUTPUT);
		digitalWrite(37, LOW);
	
		// relay 2 power/gnd (rear)
		pinMode(39, OUTPUT);
		digitalWrite(39, LOW);
		pinMode(53, OUTPUT);
		digitalWrite(53, HIGH);
	}
	
	// relay 3 is powered by jumpers on the arduino screw terminal board
	// 2 is GND, 7 is Vcc
	if (debuggingActive) Serial.println("Done.");
	
	// reset all oneshot/toggle/debounce bits before use
	if (debuggingActive) Serial.print("Resetting logic states...");
	for (uint8_t i=0; i<32; i++)
	{
		oneShotBits[i] = 0;				// general use oneshot bits
		oneShotBits[i+32] = 0;			// fault oneshot bits
		//debounceInSession[i] = 0;		// for speed, so we only update debounce timers when needed
		//debounceMemory[i] = 0;		// make function calls smaller by remembering previous output state
		faultFlags[i] = 0;				// fault bits
	}
	for(uint8_t i=0; i<sizeof(oneShotBits); i++) oneShotBits[i] = 0;
	if (debuggingActive) Serial.println("Done.");
	
	// reset all fault flags
	for(uint8_t i=0; i<sizeof(faultFlags); faultFlags[i++] = 0); 
	
	/*// load EEPROM values
	Serial.print("Loading initial eeprom values...");
	for (uint8_t i=0; i<sizeof(eepromAddress); i++) eepromBuffer[i] = eeprom_read_float(eepromAddress[i]);
	Serial.println("Done.");*/
	
	setupTime = millis() - setupTime;
	if (debuggingActive) Serial.println("\nSETUP COMPLETE in " + String(setupTime) + "ms\n");
	
	// update IO before starting main cycle
	MapInputs(1);
	MapOutputs(1);
	
	last_cycleStart = millis();
	last_cycleStartus = micros();
	if (debuggingActive) Serial.println("Beginning first scan");
}

void loop()		
{
	ONSTracker = 0;
	// debounceTracker = 0;
	timerTracker = 0;
	
	// IO updates at 50hz
	boolean updateIOPulse = oneShot(FlasherBit(50), ONSTracker++);
	MapInputs(updateIOPulse);				// routine io updates done when io pulse true
	MapOutputs(updateIOPulse);				// routine io updates done when io pulse true
	// both are PET, because the serial is updated on a NET of a 50Hz pulse, so IO and serial updates are staggered
	// speedometer PX needs to be updated FAST	
		
	LightRoutine();							// sets the status of lights on front and rear relay boards using pointers
	
	// only update clock if there is 5V aux available
	clockUpdate();
	
	DriveSystem();							// determines if it is safe to move the vehicle, and if so, generates a throttle value accordingly
	
	MonitorSystem();						// monitors analog inputs for voltage and current readings, and front wheel speed
	
	if (nextionEnabled) HMIControl();		// displays data collected in DriveSystem and MonitorSystem and converts it into strings and sends data to Nextion
	
	if (debuggingActive) debugRoutine();	// temporary fixes and misc message generation for debugging purposes
	
	Faults();								// sets fault flags based on system status
	
	if (debuggingActive && firstScan) Serial.println("First scan complete.");
	if (firstScan) firstScan = 0;
	
	delayMicroseconds(500);	// for stability
}

// SUBROUTINES
void MapInputs(boolean IOUpdate)	
{
	
	if (IOUpdate) 
	{
		for (uint8_t i=0; i<sizeof(opto1); i++)  opto1[i] = !digitalRead(opto1pins[i]);
		for (uint8_t i=0; i<sizeof(opto2); i++)  opto2[i] = !digitalRead(opto2pins[i]);
		*optoPower = !*optoPower;	// *optoPower is high when on, so need to re-invert input

		// MapInputs is read at 50Hz, so anything that is not throttleInput is done one at a time for speed
		if (analogInputTracker >= sizeof(analogInputs) / 2)
		{
			analogInputTracker = 1;
			last_analogCycleComplete = millis();
		}
		analogInputs[0] = analogRead(analogInputPins[0]);
		analogInputs[analogInputTracker] = analogRead(analogInputPins[analogInputTracker]);
		analogInputTracker++;
	}
	
	speedoPXInput = !digitalRead(speedoPXInputPin);	// this pin needs to update as fast as it can
	
}

void MapOutputs(boolean IOUpdate)	
{
	if (IOUpdate)
	{
		// outputs are active low
		if (auxPower || debuggingActive)
		{
			for (uint8_t i=0; i<sizeof(relayR1); i++) digitalWrite(relayR1Pins[i], !relayR1[i]);
			for (uint8_t i=0; i<sizeof(relayF2); i++) digitalWrite(relayF2Pins[i], !relayF2[i]);
			for (uint8_t i=0; i<sizeof(relayM3); i++) digitalWrite(relayM3Pins[i], !relayM3[i]);
		}
		else
		{
			for (uint8_t i=0; i<sizeof(relayR1); i++) digitalWrite(relayR1Pins[i], 1);
			for (uint8_t i=0; i<sizeof(relayF2); i++) digitalWrite(relayF2Pins[i], 1);
			for (uint8_t i=0; i<sizeof(relayM3); i++) digitalWrite(relayM3Pins[i], 1);
		}
		analogWrite(throttleOutputPin, throttleOutput);
		
		// repeat the throttleOutput DC as a PWM for demonstration purposes
		if (!inGear) pwmThrottleOutput = 1000;
		else pwmThrottleOutput = map(throttlePercent, 0, 100, 1100, 2000);
		zzpwmMotor.writeMicroseconds(pwmThrottleOutput);
	}
}

void LightRoutine()			
{
	if (!*lightsOn)
	{
		*FLTurn = *RLTurn = *FRTurn = *RRTurn = 0;
	}
	else if (*leftTurnInput && *rightTurnInput)
	{
		*FLTurn = *RLTurn = *FRTurn = *RRTurn = FlasherBit(1.5);
	}
	else if (*leftTurnInput)
	{
		*FLTurn = *RLTurn = FlasherBit(1.5);
		*FRTurn = 1;
		*RRTurn = 0;
	}
	else if (*rightTurnInput)
	{
		*FRTurn = *RRTurn = FlasherBit(1.5);
		*FLTurn = 1;
		*RLTurn = 0;
	}
	else // front turn signals are on at idle on motorcycles
	{
		*FLTurn = *FRTurn = 1;
		*RLTurn = *RRTurn = 0;
	}
	
	// headlight
	*lowBeamsOut = *lowBeamInput && *lightsOn;
	*highBeamsOut = *highBeamInput && *lightsOn;
	
	// brake light
	*brakeHighOutput = ((*rearBrake || *frontBrake) && *lightsOn);
	*brakeLowOutput =  *lightsOn;
	
	// fog lights
	*fogLightsOut = *fogLightsIn;
	
	// just repeat the horn out to the BOI
	*hornOutput = *hornInput;
}

void DriveSystem()			
{
	// fixes bug where exiting gear with the pb throws a fault
	if (inGear && *startPb) exitingGear = 1;
	if (exitingGear && !*startPb) exitingGear = 0;
	
	// in/out of gear logic
	if (!killswOffSinceBoot || !*killswitch) inGear = 0;
	else if (!inGear && throttlePercent > 2);	// do NOT go into gear unless throttle is idle
	else inGear = toggleState(*startPb, inGear, ONSTracker);
	ONSTracker++; // this must be incremented EVERY scan
	
	// check if killswitch has been off since boot
	if (!killswOffSinceBoot && !*killswitch) killswOffSinceBoot = 1;
	
	// control logic for the ESC solenoid
	if (!killswOffSinceBoot) *ESCSolenoid = 0;
	else if (contactorSafetiesActive && *anyLevel1FaultDetected) killswOffSinceBoot = 0;
	else *ESCSolenoid = *killswitch;
	
	throttlePercent = map(*throttleInput, voltsToAnalogIn(1), voltsToAnalogIn(4), 0, 100);		// calculate the pulse width in us for motor out
	
	if (inGear) throttleOutput = map(*throttleInput, voltsToAnalogIn(1), voltsToAnalogIn(4), voltsToAnalogOut(1), voltsToAnalogOut(4));
	else throttleOutput = voltsToAnalogOut(1);
	
	if (sportMode) 
	{
		*speedHighOut = 1; 
		*speedLowOut = 0;
	}
	else if (economyMode)
	{
		*speedHighOut = 0;
		*speedLowOut = 1;
	}
	else
	{
		*speedHighOut = 0;
		*speedLowOut = 0;
	}
	
	return;
}

void MonitorSystem()		
{
	
	// reset watchdog timer
	watchdog = millis() - last_cycleStart;
	last_cycleStart = millis();
	
	// check for fastest/longest cycle
	if (watchdog > longestCycle) longestCycle = watchdog;
	if (watchdog < fastestCycle) fastestCycle = watchdog;
	
	// value calculated based on what ina126p output should be
	currentDrawShuntmA = map(*currentDrawInput, 0, voltsToAnalogIn(4.425), 0, 15000); // calculates a precise float in ma
	currentDrawMotorAmps = map(*motorDrawInput, 0, voltsToAnalogIn(4.25), 0, 150); // calculates a precise float in amps
	for (uint8_t i=0; i < sizeof(cellVolts) / 4; i++) cellVolts[i] = (float)map(*cellVoltageRawIn[i], 0, 648, 0, 1512) / 100.0;	// calculates a precise cell level in volts
	vBat = (float)(map(*vBatInput, 0, 570, 0, 5992)) / 100.0;
	
	// draw in mAh to be added is draw * 0.2778 = (mAh in 0.5s at draw rate in mA)
	if (oneShot(FlasherBit(2), ONSTracker++)) totalDraw_mAh += (int)(currentDrawMotorAmps * 0.1389);		// calculation done in Amps
	/*
		10 A for an hour is 10000mAh
		for a second is 2.778mAh
		for half a second is 1.389mAh
		Therefore, for each amp drawn, 0.1389mAh is expended in 0.5s
	*/
	
	// keep track of how many seconds the system has been in gear
	if (oneShot(FlasherBit(1), ONSTracker++) && inGear) totalInGearSeconds++;
	
	// SPEED LOGIC
	if (oneShot(speedoPXInput, ONSTracker++)) speedCount++;
	if (oneShot(FlasherBit(2), ONSTracker++))
	{
		speed = map(speedCount, 0, 50, 0, 101);
							// 50 pulses in 0.5s is 101km/h
		if (speedDebugActive)
		{
			Serial.println("speed is " + String(speed) + "km/h");
			Serial.println("speedCount is " + String(speedCount));
		}						
		speedCount = 0;	
	}
	/*	speed is an integer representing speed in km/h
		front wheel has 8 spokes on the brake
		front wheel has a 70 cm OD
		c = pi * 70
		each PET = c/8 cm traveled
		I will use the time between PETs to calculate the speed
		At 100kph, the wheel rotates at 12.64rps
		That is 101 pulses per second, meaning we need at least 200-300 samples per second
		
		101 pulses per second at 100kph
		10ms between each PET
		Likewise, 25kph would be 40ms between each pulse
		We will use a map() function with these two points to calculate the speed, using the micros() function, for accuracy
	*/
		
}
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

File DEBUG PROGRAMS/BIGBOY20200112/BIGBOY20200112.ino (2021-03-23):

/*
    Name:       BIGBOY20200112.ino
    Created:	2020-01-12 7:41:47 PM
    Author:     COLE-VM\colefuerth
	
	DEMO PROGRAM FOR TESTING SOFTWARE AND COMMS
	
	Goals of this demo:
	- read potentiometer value as 0-100% on main and display on HMI, as well as on LEDs
	- Read inductive sensor value and forward value to HMI, as well as the relay
	- Button will toggle in/out of gear; status will be displayed on LED as well as make an icon appear/disappear on HMI for neutral/drive
	- Store in/out of gear status on sdcard; restore previous state when booting next time
	- do some kind of integral to keep track of current draw from motor in gear and track it in sdcard
	- have console logging for debug, as well as sdcard logging
	
	
	NOTES
	- add serial logic and monitoring system logic; most hardware logic from the standard is done as far as I can see
	- probably still some standard logic missing but thats ok ill add it as it pops up
	- might do logging of console and sdcard, and make logic so it sends a string as a parameter for a call, and decide in the call whether to send the string to console or not to avoid all the waiting for that shit
	- NEEDS ALARMS OF SOME KIND
	- should probably do an interface so I can tune everything from the HMI to make setting up 600 times faster
*/

// clock library
#include <Wire.h>
// sdcard libraries
#include <SPI.h>
#include <SD.h>

#include <DS3231.h>		// RTC library

//#include "SerialTransfer-master/SerialTransfer.h"
//SerialTransfer myTransfer;

// IO variables
int potentiometer; 
int throttlePercent;
boolean leds[8];
boolean gearInd;
int transmissionBuffer[10];  
boolean proxStatus;
boolean buttonInput;
boolean button1;

// debounce variables:
boolean inGearButton, button1mem;
int button1Debounce;

// modes variables
boolean inGear, inGearONS;

// monitorSystem variables
int currentDraw, lastDrawUpdate;
float totalDraw_mAh;
int watchdog, last_cycleStart, longestCycle, fastestCycle;
// int watchdog_Buffer[20];		//zzz	will be used for debug later

// ClockRoutine variables
int lastClockRefreshTime;
RTClib RTC;
DateTime now;

// declare pin values
const int inGearIndPin = 17;
const int ledPins[8] = {15,14,2,3,4,5,6,7};
const int potentiometerPin = PIN_A0;
const int relayOutput = 52;
const int proxPin = 53;
const int button1Pin = 21;




void setup()
{
	
	Serial.begin(9600);	// computer comms
	Serial.write("serial communication initiated");
/*
	if (Serial.write_error())
	{
		logging("serial 0 communication init failed, disabling serial comms");	//zzz maybe create logic to turn off attempts to log to serial if serial fails?
		Serial.end();
	}
*/
	// fetch the current date and time before any other functions, for logging:
	Wire.begin();
	Serial.println("Wire initialized");
	lastClockRefreshTime = millis();
	now = RTC.now();
	// Serial.println
	
	pinMode(inGearIndPin, OUTPUT);
	
	for (int i=0; i<8; i++)
	{
		pinMode(ledPins[i], OUTPUT);
	}
	
	// reset transmission buffer
	for (int i=0; i>10; i++)	
	{
		transmissionBuffer[i] = 0;
	}
	
	// set initial modes
	inGearONS = 0;
	inGear = 0;
	
	// reset monitor system for session
	totalDraw_mAh = 0;
	fastestCycle = 1000;
	longestCycle = 0;

}

void loop()
{
	// call all functions in a loop here
	MapInputs();
	Modes();
	MonitorSystem();
	SDCard();
	SerialComms();
	MapOutputs();
	
	delay(5);	// for stability in a low demand program
}

void MapInputs()
{
	int currentTime = millis();		// temp variable to check the time only once at the beginning of any call that needs it
	
	proxStatus = digitalRead(proxPin);
	potentiometer = analogRead(potentiometerPin);
	
	
	// input from button1
	button1 = !digitalRead(button1Pin);	// pullup, so inverting input
	
	// debounce button1 and output debounced bit to inGearButton
	if (button1 != button1mem){
		button1mem = button1;
		button1Debounce = currentTime;
	}
	if (currentTime - button1Debounce > 20) inGearButton = button1;
}

void Modes()
{
	// toggle logic for in/out of gear
	if (inGearButton == 1 && inGearONS == 0){
		inGear = !inGear;
		inGearONS = 1;
	}
	else if (inGearButton == 0 && inGearONS == 1) inGearONS = 0;
	else;
}

void MonitorSystem()
{
	int currentTime = millis();	// for cycle speed
	
	// reset watchdog timer
	watchdog = currentTime - last_cycleStart;
	last_cycleStart = currentTime;

	// check for fastest/longest cycle
	if (watchdog > longestCycle) longestCycle = watchdog;
	if (watchdog < fastestCycle) fastestCycle = watchdog;
	
	// add logic for monitoring cycles per second
	throttlePercent = map(potentiometer, 0, 1023, 0, 100);		// integer 0-100 for throttle position
	float currentPercent = pow((float)throttlePercent / 100, 2);// returns a float 0-1 with a quadratic curve for currentPercent
	float j = currentPercent * 200;								// stores the float value for current draw in a temp variable
	currentDraw = (int)currentPercent;							// converts temporary current draw to an integer value, 0-200A draw
	
	// need to make an integral to keep track of total draw in mAh
	// all calculations will be done with floats for precision
	// draw in mAh to be added is draw * 0.2778 = (mAh in 0.5s at draw rate)
	if (currentTime - lastDrawUpdate >= 500)	// update total draw at 2Hz
	{
		totalDraw_mAh += j * 0.2778;
		lastDrawUpdate = currentTime;
	}
	
	
}

void ClockRoutine()
{
	
	int currentTime = millis();
	
	if (currentTime - lastClockRefreshTime >= 1000){		// refresh date and time every second
		
		lastClockRefreshTime = currentTime;
		now = RTC.now();
		
		
		/*		// for now I'lll just use now.year(), etc
		nowYear = now.year();
		nowMonth = now.month();
		nowDay = now.day();
		nowHour = now.hour();
		nowMinute = now.minute();
		nowSecond = now.second();
		*/
	}
	
}

void SDCard()
{
	
}

void SerialComms()
{
	// serial communications between master and HMI CPUs are done here
	
	
	
	
}

void MapOutputs()
{
	// led outputs:
	for (int i=0; i<8; i++)
	{
		digitalWrite(leds[i], ledPins[i]);
	}
	
	// display in gear status to output pin
	digitalWrite(inGear, inGearIndPin);
}


// function calls
void logging(String input_data)
{
	Serial.println(input_data);
	// add logic to store events in SDCard
}

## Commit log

2021-03-23 Final Submission Backup
    [BOM.xlsx, Bill of Materials in Report.xlsx, Bill of Materials.xlsx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]
2021-10-06 Added photos of project, project proposal from beginning of project, and the final presentation powerpoint.
